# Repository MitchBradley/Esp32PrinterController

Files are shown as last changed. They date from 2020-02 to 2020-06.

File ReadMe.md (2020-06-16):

# ESP32 3D Printer Controller

This is based on https://github.com/felixstorm/Creality_Ender_3_ESP32_Board.git with the following changes

- Laid out for 2-sided PCB fabrication instead of PCB routing.  2-sided PCBs are available at very low cost from various prototyping shops, and provide much better grounding and power distribution.
- Can use either Pololu stepper driver modules or external drivers, selected by solder jumpers.
- The microstepping ratio can be selected by solder jumpers, or those pins can be connected to SPI for fine-grained configuration of TMC modules.  The X Y and Z axes all use the same microstepping/SPI settings, whereas the extruder can be configured independently of X, Y, Z.
- The I/O voltage to the shift registers and stepper modules can be either 3V3 or 5V, selected by solder jumper.  3V3 is appropriate for TMC modules where the SPI output goes back to the ESP32.  5V is best for external drivers whose optocoupler inputs work best at 5V.  Non-TMC stepper modules can use either.
- The micro SD card socket uses a Wemos D1 Mini shield which has a smaller footprint than the one on the original design, permitting all the drivers to be placed along one edge of the board.
- The connectors along the bottom edge of the board, and the power input connector, are all pluggable terminal blocks, thus permitting easy disconnection of the signals for assembly and maintenance.  The layout permits each signal pair to be on its own plug, or everything on one longer plug, or any combination thereof, at the users discretion.
- For the steppers, you can choose either 0.1" pitch connectors - e.g. pin headers with Dupont connectors - or 0.15" pitch pluggable terminal blocks (or 0.15" screw terminals, but pluggable is easier to wire and maintain).
- The fuse holders were spread out to make it easier to get your fingers in to grab the fuses.

The design passes acceptance checks for the aisler.net entry level prototyping service.

Update: The board is fully functional.  If you would like to build it, contact me and I will upload the revised version that fixes a few silkscreen errors and provides better clearance between some components that were a little crowded.

*Yet another Update:  Do not use the fan outputs; they are broken.  If you connect a fan it is likely to blow up the ULN2803A chip.  The problem - which I inherited from the base design and neglected to check - is that you cannot put ULN2803A channels in parallel and get them to share current.  ULN2803A use bipolar junction transistors - BJTs.  BJTs have a positive temperature coefficient, which means that, as the temperature increases, the collector current also increases.  When you put them in parallel, if one of them starts drawing a little more current than its neighbor, it gets hotter, and starts drawing even more current.  This is called "thermal runaway". Instead of sharing the load, one will take it all, then overheat and blow out, then the neighbor will take all the current and blow out, etc.  It is possible to make current-sharing circuits with BJTs, but ULN2803A does not have that kind of circuit.  The solution to the problem is to replace the ULN2803A with MOSFETs like that one that controls the extruder temperature.*

The board works with Marlin 2.0 for printer applications and with [Grbl_ESP32](https://github.com/bdring/Grbl_Esp32) for general CNC.

ESP32PrinterBoard

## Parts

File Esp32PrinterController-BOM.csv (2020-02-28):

Id | Designator | Package | Quantity | Designation | Supplier and ref
1 | J11 | PhoenixContact_MSTBVA_2,5_2-G-5,08_1x02_P5.08mm_Vertical_WallToWall | 1 | +BED-
2 | J1 | PhoenixContact_MSTBVA_2,5_2-G-5,08_1x02_P5.08mm_Vertical_WallToWall | 1 | -24V IN+
3 | J20 | PhoenixContact_MSTBVA_2,5_2-G-5,08_1x02_P5.08mm_Vertical_WallToWall | 1 | +BT-
4 | J21 | PhoenixContact_MSTBVA_2,5_2-G-5,08_1x02_P5.08mm_Vertical_WallToWall | 1 | +NT-
5 | J30 | PhoenixContact_MSTBVA_2,5_2-G-5,08_1x02_P5.08mm_Vertical_WallToWall | 1 | +XM-
6 | J31 | PhoenixContact_MSTBVA_2,5_2-G-5,08_1x02_P5.08mm_Vertical_WallToWall | 1 | +YM-
7 | J32 | PhoenixContact_MSTBVA_2,5_2-G-5,08_1x02_P5.08mm_Vertical_WallToWall | 1 | +ZM-
8 | J10 | PhoenixContact_MSTBVA_2,5_2-G-5,08_1x02_P5.08mm_Vertical_WallToWall | 1 | +NOZ-
9 | J12 | PhoenixContact_MSTBVA_2,5_2-G-5,08_1x02_P5.08mm_Vertical_WallToWall | 1 | +FAN1-
10 | J13 | PhoenixContact_MSTBVA_2,5_2-G-5,08_1x02_P5.08mm_Vertical_WallToWall | 1 | +FAN2-
11 | J14 | PhoenixContact_MSTBVA_2,5_2-G-5,08_1x02_P5.08mm_Vertical_WallToWall | 1 | +FAN3-
12 | U1 | MODULE_ESP32-DEVKITC-32D_LongPads | 1 | ESP32-DEVKITC-32D
13 | J60 | PinHeader_2x04_P2.54mm_Vertical | 1 | BLTouch
14 | J40 | PinHeader_2x05_P2.54mm_Vertical | 1 | LCD
15 | Q1 | TO-220-3_Vertical | 1 | IRLZ44N
16 | Q2 | TO-220-3_Vertical | 1 | IRLB8743
17 | JP15,JP2,JP3,JP4,JP5,JP6,JP7,JP10,JP11,JP12,JP13,JP14,JP16,JP17,JP18,JP19,JP20,JP21 | SolderJumper-2_P1.3mm_Open_TrianglePad1.0x1.5mm | 18 | SolderJumper_2_Open
18 | A2 | Pololu_Breakout-16_15.2x20.3mm | 1 | DRIVER_Y
19 | R16,R11 | R_Axial_DIN0207_L6.3mm_D2.5mm_P10.16mm_Horizontal | 2 | 100k
20 | D2 | LED_D5.0mm | 1 | NOZ
21 | D3 | LED_D5.0mm | 1 | BED
22 | R17,R12 | R_Axial_DIN0207_L6.3mm_D2.5mm_P10.16mm_Horizontal | 2 | 2.2k
23 | R15,R10 | R_Axial_DIN0207_L6.3mm_D2.5mm_P10.16mm_Horizontal | 2 | 10
24 | C4,C2,C21,C23,C30,C160,C32,C170,C31,C8,C9,C10,C11 | C_Rect_L7.2mm_W2.5mm_P5.00mm_FKS2_FKP2_MKS2_MKP2 | 13 | 0.1uF
25 | R22,R20 | R_Axial_DIN0207_L6.3mm_D2.5mm_P10.16mm_Horizontal | 2 | 4.7k
26 | H3,H4,H1,H2 | MountingHole_3mm | 4 | MountingHole
27 | D1 | D_DO-35_SOD27_P10.16mm_Horizontal | 1 | 1N5819
28 | U2 | Module_LM2596_DC-DC | 1 | DcStepDown_LM2596
29 | R30,R31,R32 | R_Axial_DIN0207_L6.3mm_D2.5mm_P10.16mm_Horizontal | 3 | 10k
30 | J6 | PhoenixContact_MCV_1,5_4-G-3.81_1x04_P3.81mm_Vertical | 1 | MOT E
31 | J25 | PhoenixContact_MCV_1,5_4-G-3.81_1x04_P3.81mm_Vertical | 1 | MOT X
32 | J26 | PhoenixContact_MCV_1,5_4-G-3.81_1x04_P3.81mm_Vertical | 1 | MOT Y
33 | J27 | PhoenixContact_MCV_1,5_4-G-3.81_1x04_P3.81mm_Vertical | 1 | MOT Z
34 | JP1 | SolderJumper-3_P2.0mm_Open_TrianglePad1.0x1.5mm_NumberLabels | 1 | Jumper_3_Open
35 | U6 | WEMOS_D1_mini_light | 1 | WeMos_D1_mini_SD_Shield
36 | JP8,JP9,JP22,JP23,JP24,JP25,JP26,JP27 | SolderJumper-3_P1.3mm_Open_RoundedPad1.0x1.5mm_NumberLabels | 8 | Jumper_3_Open
37 | J5 | PinHeader_1x04_P2.54mm_Vertical | 1 | MOT E
38 | J23 | PinHeader_1x04_P2.54mm_Vertical | 1 | MOT Y
39 | J24 | PinHeader_1x04_P2.54mm_Vertical | 1 | MOT Z
40 | A3 | Pololu_Breakout-16_15.2x20.3mm | 1 | DRIVER_Z
41 | A4 | Pololu_Breakout-16_15.2x20.3mm | 1 | DRIVER_E
42 | C5,C6,C7,C110,C1 | CP_Radial_D6.3mm_P2.50mm | 5 | 100uF
43 | C22,C20 | CP_Radial_D5.0mm_P2.00mm | 2 | 4.7uF
44 | A1 | Pololu_Breakout-16_15.2x20.3mm | 1 | DRIVER_X
45 | C3 | CP_Radial_D7.5mm_P2.50mm | 1 | 100uF
46 | F1 | Fuseholder_Blade_ATO_Littelfuse_Pudenz_2_Pin | 1 | 3A REM
47 | F2 | Fuseholder_Blade_ATO_Littelfuse_Pudenz_2_Pin | 1 | 10A BED
48 | J110 | PinHeader_1x04_P2.54mm_Vertical | 1 | MOT X
49 | U3,U4 | DIP-16_W7.62mm_Socket_LongPads | 2 | 74AHCT595
50 | U5 | DIP-18_W7.62mm_Socket_LongPads | 1 | ULN2803A

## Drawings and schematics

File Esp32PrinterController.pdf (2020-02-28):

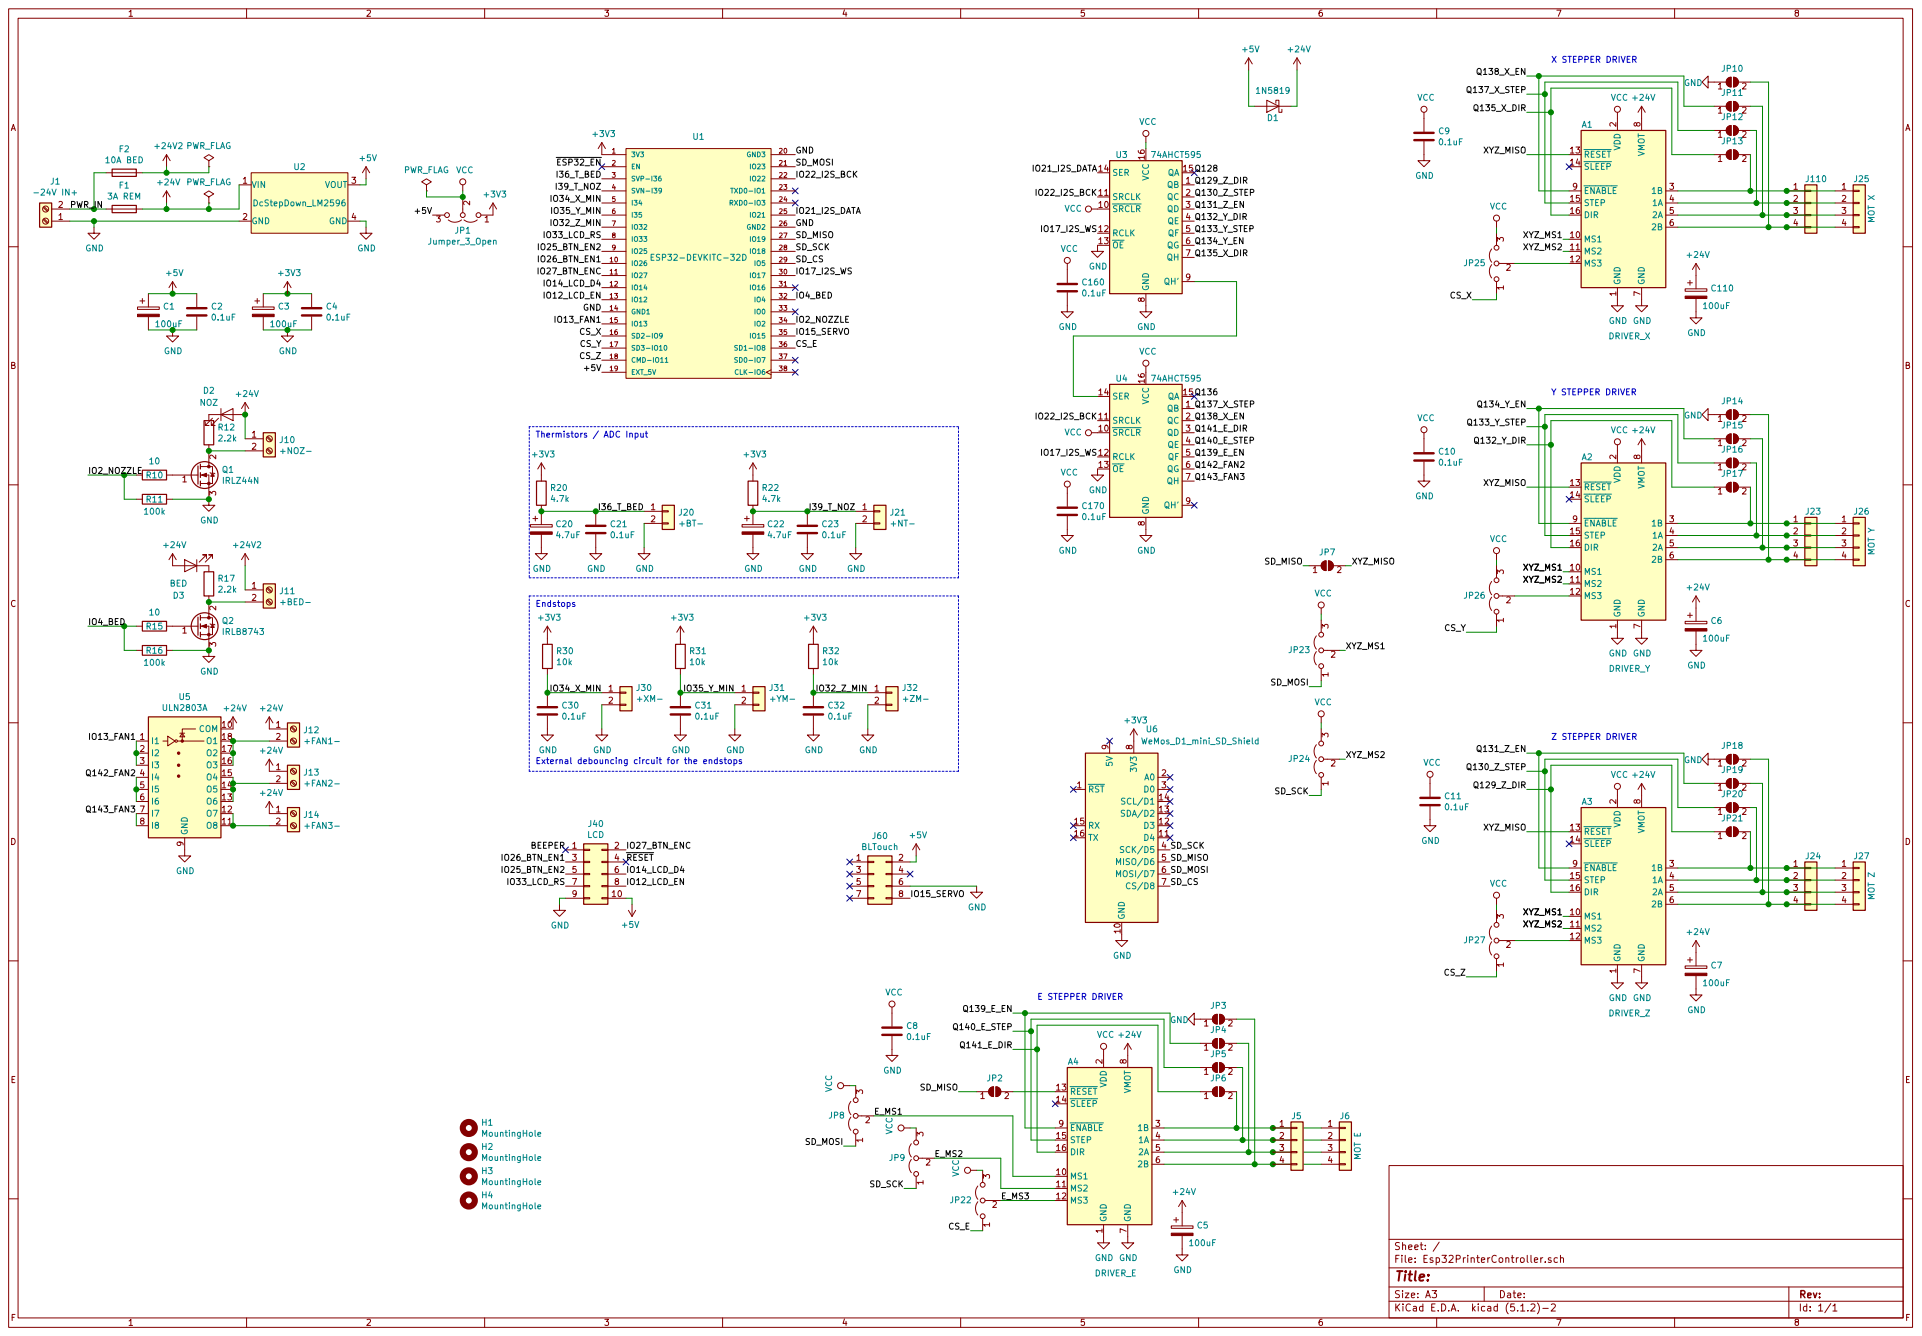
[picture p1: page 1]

1 MS1 10 MS2 11 MS3 12 RESET 13 SLEEP 14 STEP 15 DIR 16 VDD

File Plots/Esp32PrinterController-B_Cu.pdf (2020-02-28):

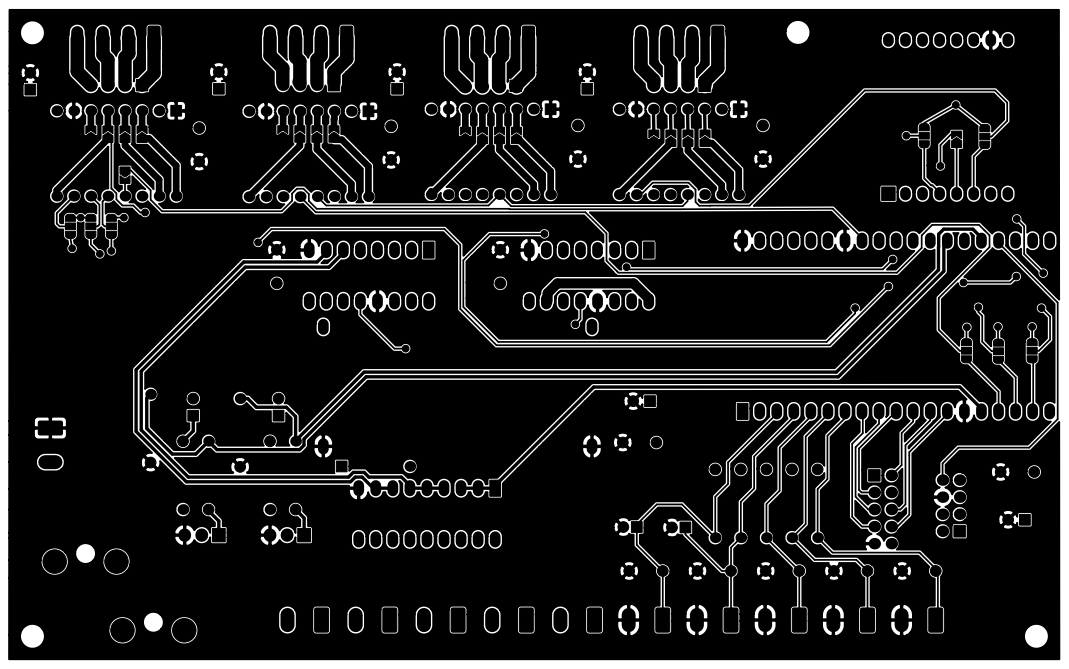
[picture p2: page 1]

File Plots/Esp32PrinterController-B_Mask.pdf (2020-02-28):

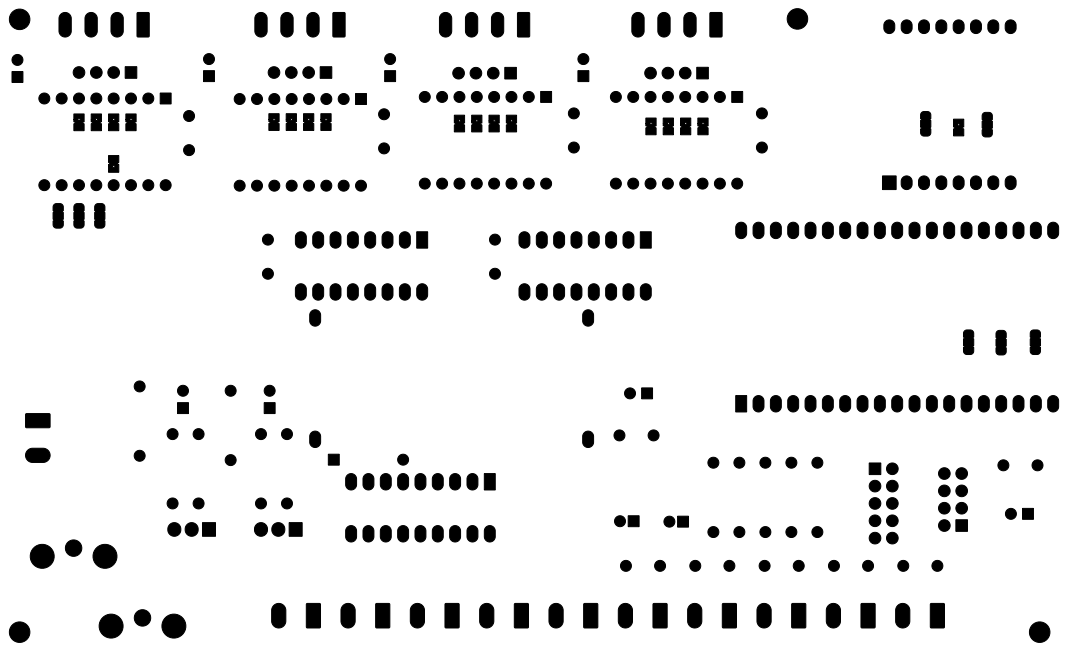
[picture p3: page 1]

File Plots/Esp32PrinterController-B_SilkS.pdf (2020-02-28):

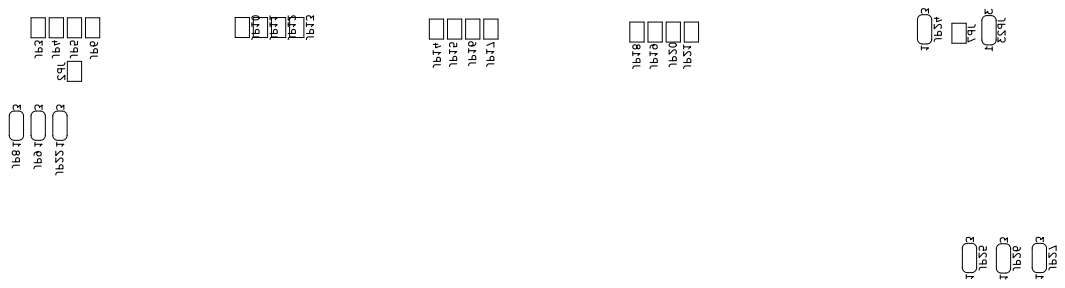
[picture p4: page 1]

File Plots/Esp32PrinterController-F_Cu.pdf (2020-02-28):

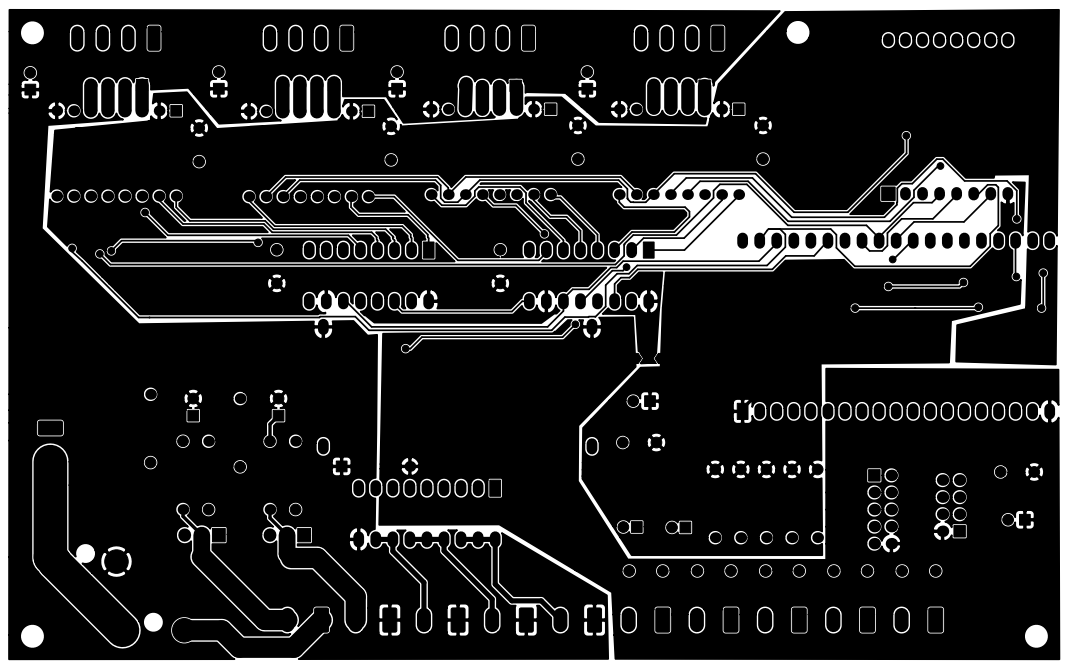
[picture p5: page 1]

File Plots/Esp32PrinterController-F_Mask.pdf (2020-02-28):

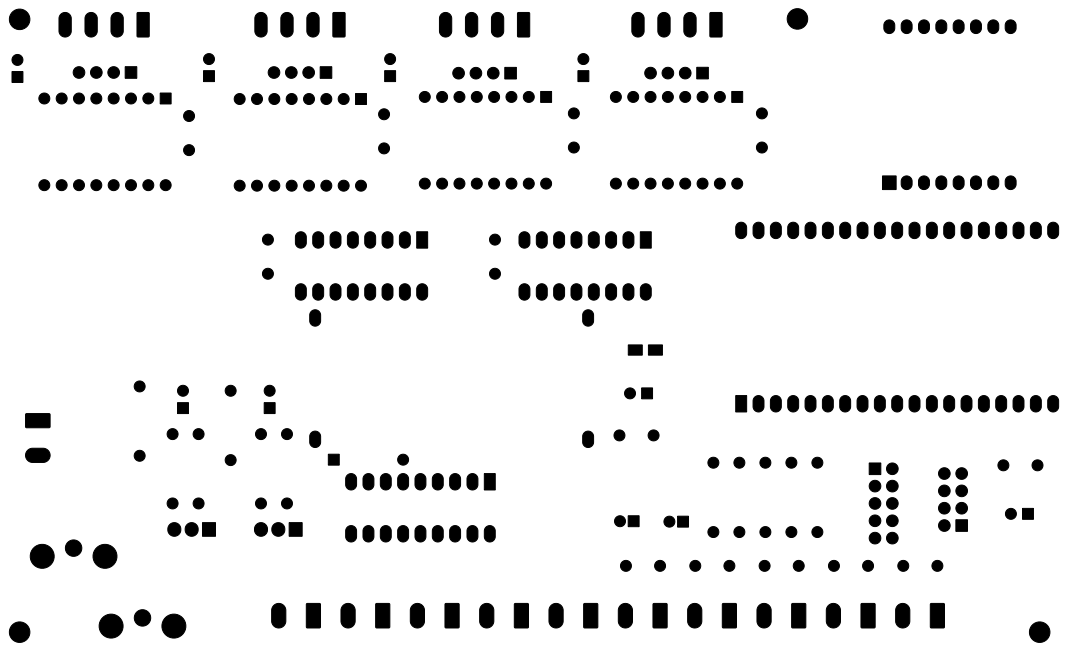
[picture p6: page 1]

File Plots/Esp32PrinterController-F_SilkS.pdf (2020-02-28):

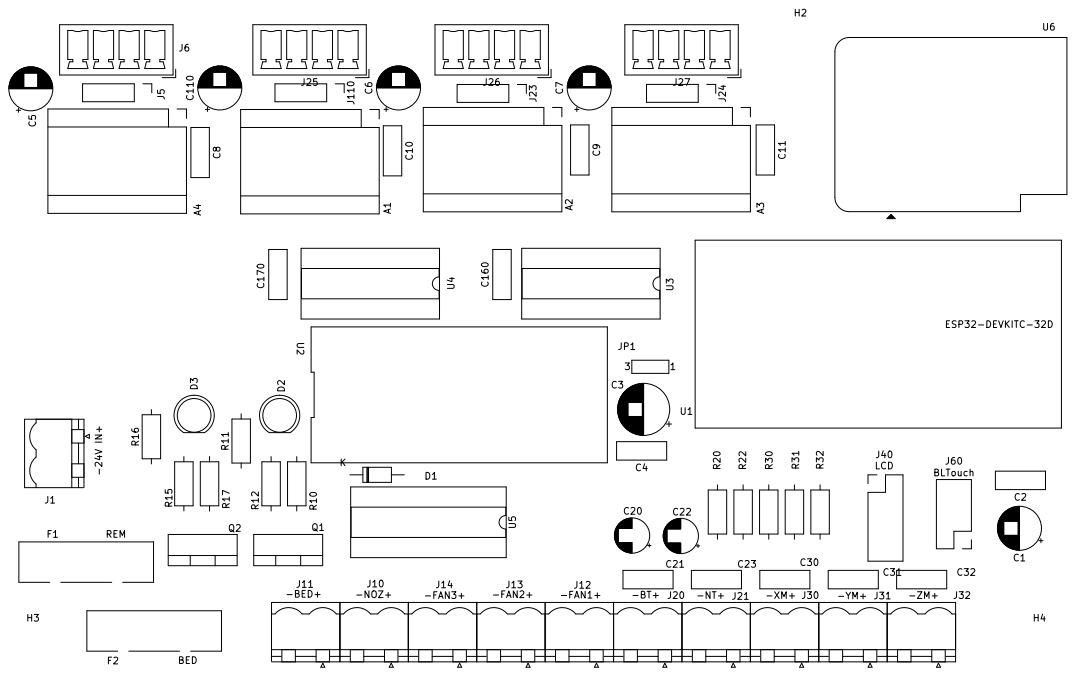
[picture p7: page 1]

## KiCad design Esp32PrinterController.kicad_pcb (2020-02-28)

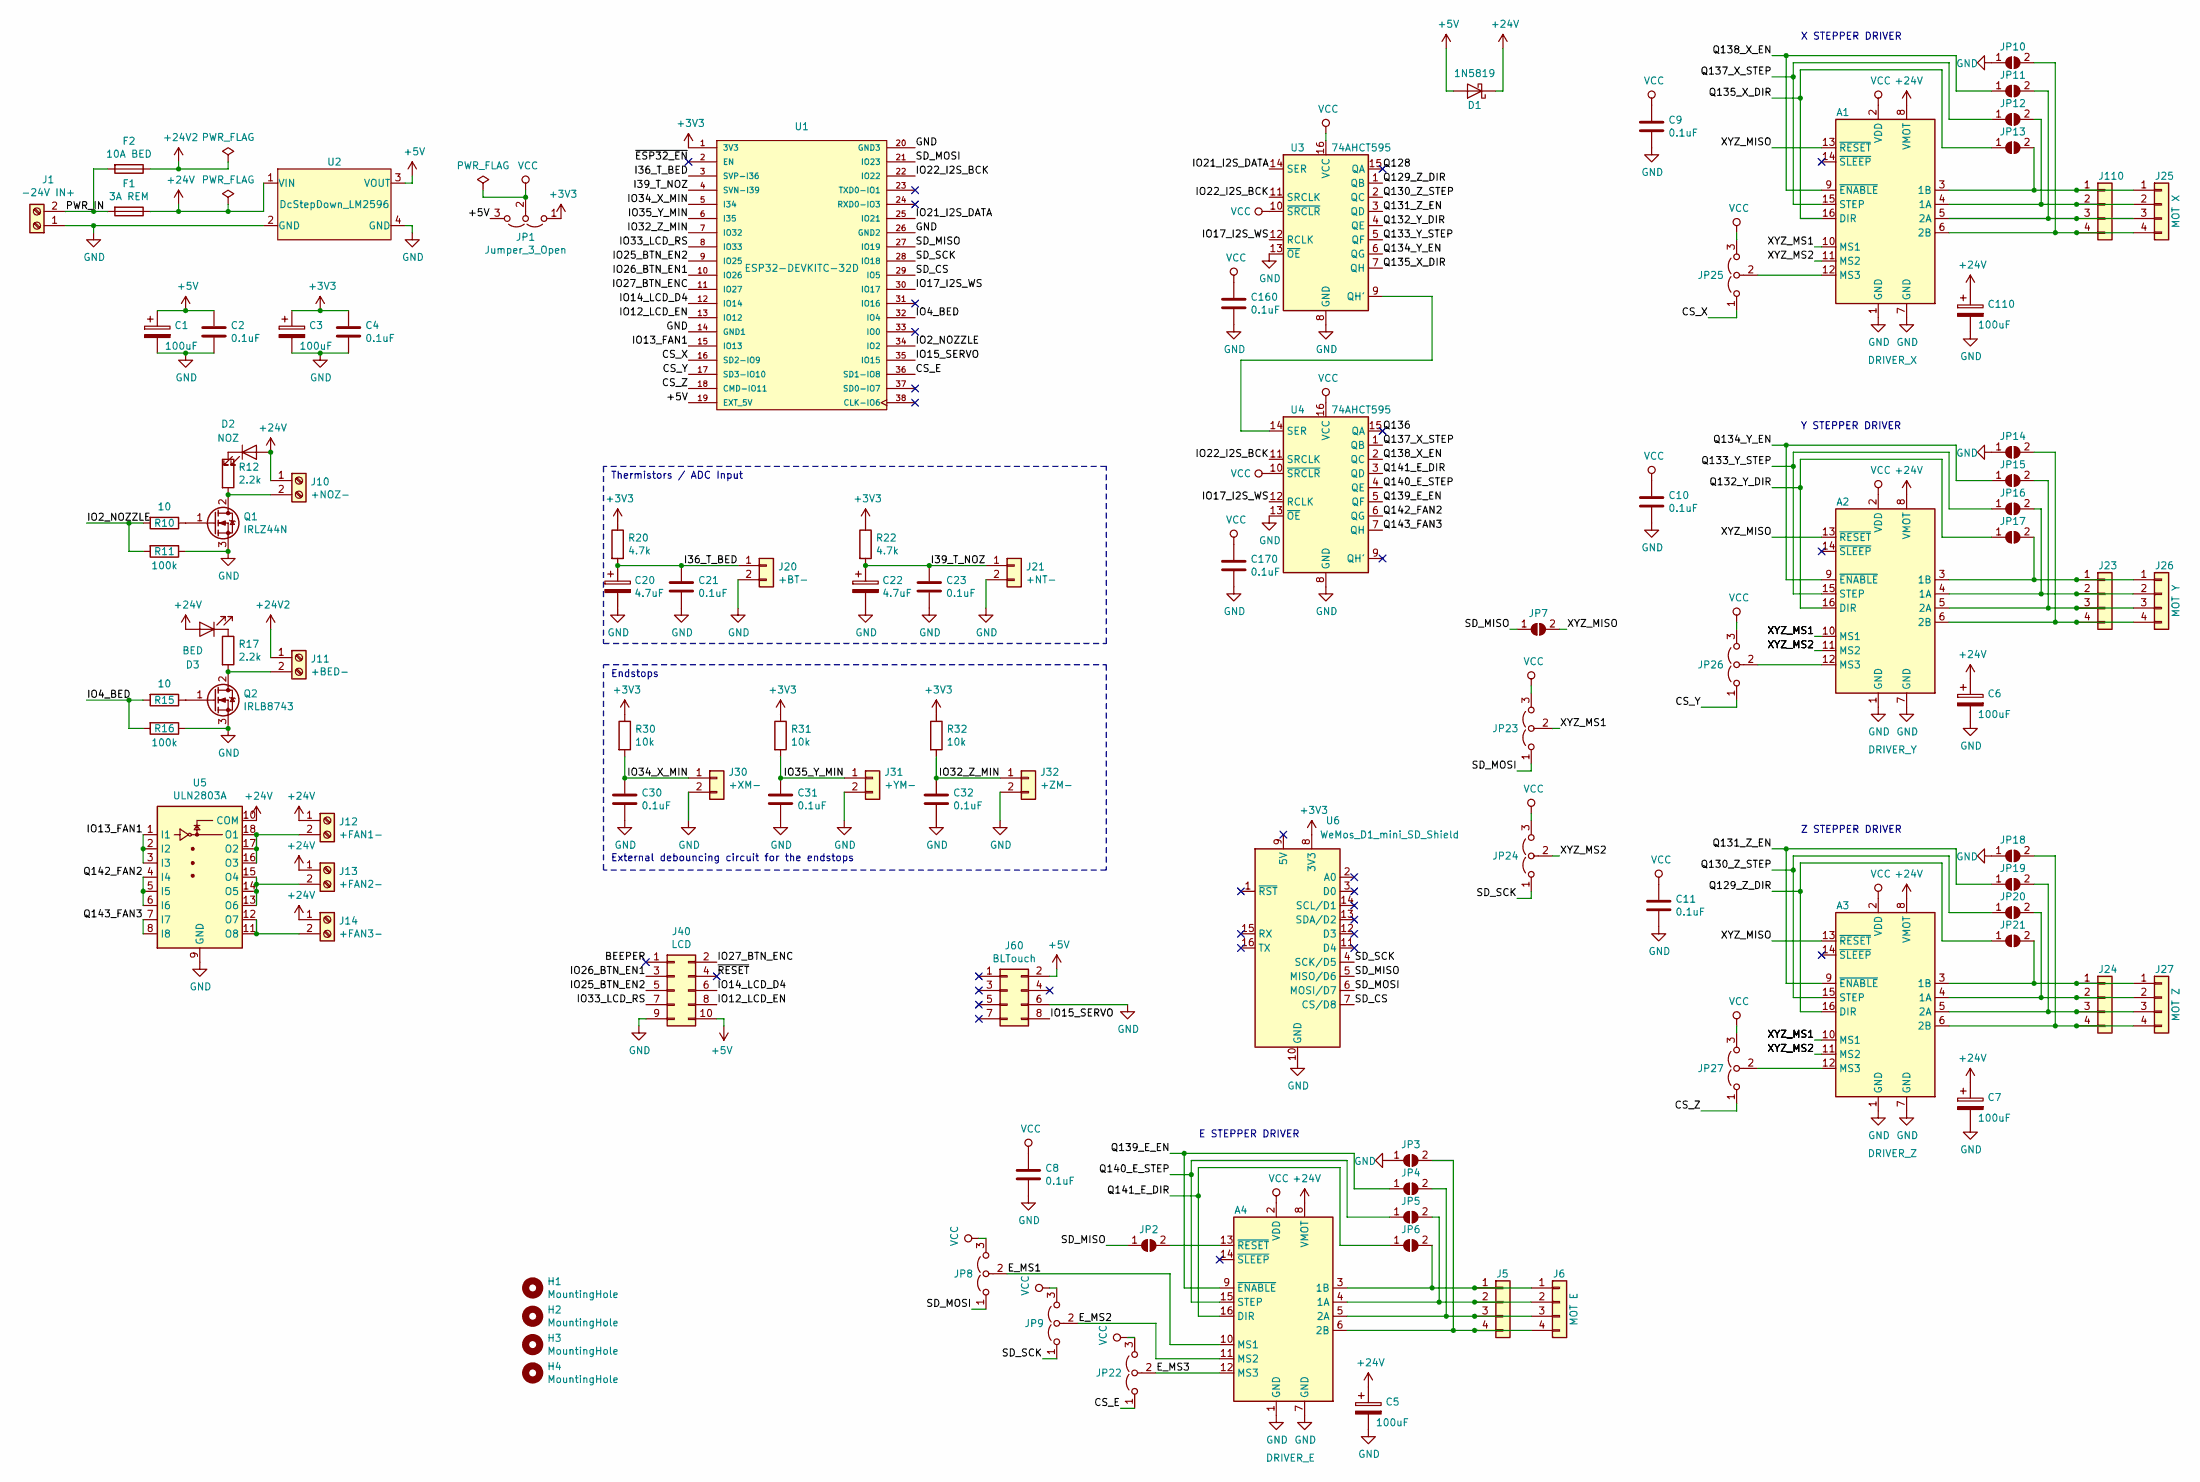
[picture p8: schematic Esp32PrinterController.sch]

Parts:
A1: DRIVER_X; Pololu_Breakout-16_15.2x20.3mm
A2: DRIVER_Y; Pololu_Breakout-16_15.2x20.3mm
A3: DRIVER_Z; Pololu_Breakout-16_15.2x20.3mm
A4: DRIVER_E; Pololu_Breakout-16_15.2x20.3mm
C1, C5, C6, C7, C110: 100uF; CP_Radial_D6.3mm_P2.50mm
C2, C4, C8, C9, C10, C11, C21, C23, C30, C31, C32, C160, C170: 0.1uF; C_Rect_L7.2mm_W2.5mm_P5.00mm_FKS2_FKP2_MKS2_MKP2
C3: 100uF; CP_Radial_D7.5mm_P2.50mm
C20, C22: 4.7uF; CP_Radial_D5.0mm_P2.00mm
D1: 1N5819; D_DO-35_SOD27_P10.16mm_Horizontal
D2: NOZ; LED_D5.0mm
D3: BED; LED_D5.0mm
F1: 3A REM; Fuseholder_Blade_ATO_Littelfuse_Pudenz_2_Pin
F2: 10A BED; Fuseholder_Blade_ATO_Littelfuse_Pudenz_2_Pin
H1, H2, H3, H4: MountingHole; MountingHole_3mm
J1: -24V IN+; PhoenixContact_MSTBVA_2,5_2-G-5,08_1x02_P5.08mm_Vertical
J5: MOT E; PinHeader_1x04_P2.54mm_Vertical
J6: MOT E; PhoenixContact_MCV_1,5_4-G-3.81_1x04_P3.81mm_Vertical
J10: +NOZ-; PhoenixContact_MSTBVA_2,5_2-G-5,08_1x02_P5.08mm_Vertical
J11: +BED-; PhoenixContact_MSTBVA_2,5_2-G-5,08_1x02_P5.08mm_Vertical
J12: +FAN1-; PhoenixContact_MSTBVA_2,5_2-G-5,08_1x02_P5.08mm_Vertical
J13: +FAN2-; PhoenixContact_MSTBVA_2,5_2-G-5,08_1x02_P5.08mm_Vertical
J14: +FAN3-; PhoenixContact_MSTBVA_2,5_2-G-5,08_1x02_P5.08mm_Vertical
J20: +BT-; PhoenixContact_MSTBVA_2,5_2-G-5,08_1x02_P5.08mm_Vertical
J21: +NT-; PhoenixContact_MSTBVA_2,5_2-G-5,08_1x02_P5.08mm_Vertical
J23: MOT Y; PinHeader_1x04_P2.54mm_Vertical
J24: MOT Z; PinHeader_1x04_P2.54mm_Vertical
J25: MOT X; PhoenixContact_MCV_1,5_4-G-3.81_1x04_P3.81mm_Vertical
J26: MOT Y; PhoenixContact_MCV_1,5_4-G-3.81_1x04_P3.81mm_Vertical
J27: MOT Z; PhoenixContact_MCV_1,5_4-G-3.81_1x04_P3.81mm_Vertical
J30: +XM-; PhoenixContact_MSTBVA_2,5_2-G-5,08_1x02_P5.08mm_Vertical
J31: +YM-; PhoenixContact_MSTBVA_2,5_2-G-5,08_1x02_P5.08mm_Vertical
J32: +ZM-; PhoenixContact_MSTBVA_2,5_2-G-5,08_1x02_P5.08mm_Vertical
J40: LCD; PinHeader_2x05_P2.54mm_Vertical
J60: BLTouch; PinHeader_2x04_P2.54mm_Vertical
J110: MOT X; PinHeader_1x04_P2.54mm_Vertical
JP1: Jumper_3_Open; SolderJumper-3_P2.0mm_Open_TrianglePad1.0x1.5mm_NumberLabels
JP2, JP3, JP4, JP5, JP6, JP7, JP10, JP11, JP12, JP13, JP14, JP15, JP16, JP17, JP18, JP19, JP20, JP21: SolderJumper_2_Open; SolderJumper-2_P1.3mm_Open_TrianglePad1.0x1.5mm
JP8, JP9, JP22, JP23, JP24, JP25, JP26, JP27: Jumper_3_Open; SolderJumper-3_P1.3mm_Open_RoundedPad1.0x1.5mm_NumberLabels
Q1: IRLZ44N; TO-220-3_Vertical
Q2: IRLB8743; TO-220-3_Vertical
R10, R15: 10; R_Axial_DIN0207_L6.3mm_D2.5mm_P10.16mm_Horizontal
R11, R16: 100k; R_Axial_DIN0207_L6.3mm_D2.5mm_P10.16mm_Horizontal
R12, R17: 2.2k; R_Axial_DIN0207_L6.3mm_D2.5mm_P10.16mm_Horizontal
R20, R22: 4.7k; R_Axial_DIN0207_L6.3mm_D2.5mm_P10.16mm_Horizontal
R30, R31, R32: 10k; R_Axial_DIN0207_L6.3mm_D2.5mm_P10.16mm_Horizontal
U1: ESP32-DEVKITC-32D; MODULE_ESP32-DEVKITC-32D_LongPads
U2: DcStepDown_LM2596; Module_LM2596_DC-DC
U3, U4: 74AHCT595; DIP-16_W7.62mm_Socket_LongPads
U5: ULN2803A; DIP-18_W7.62mm_Socket_LongPads
U6: WeMos_D1_mini_SD_Shield; WEMOS_D1_mini_light

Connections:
+3V3: C3.1, C4.1, JP1.1 (A), R20.1, R22.1, R30.1, R31.1, R32.1, U1.1 (3V3), U6.8 (3V3)
+5V: C1.1, C2.1, D1.2 (A), J40.10, J60.2, JP1.3 (B), U1.19 (EXT_5V), U2.3 (VOUT)
+24V: A1.8 (VMOT), A2.8 (VMOT), A3.8 (VMOT), A4.8 (VMOT), C5.1, C6.1, C7.1, C110.1, D1.1 (K), D2.2 (A), D3.2 (A), F1.1, J10.1, J12.1, J13.1, J14.1, U2.1 (VIN), U5.10 (COM)
+24V2: F2.1, J11.1
/BEEPER: J40.1
/CS_E: JP22.1 (A), U1.36 (SD1-IO8)
/CS_X: JP25.1 (A), U1.16 (SD2-IO9)
/CS_Y: JP26.1 (A), U1.17 (SD3-IO10)
/CS_Z: JP27.1 (A), U1.18 (CMD-IO11)
/E_MS1: A4.10 (MS1), JP8.2 (C)
/E_MS2: A4.11 (MS2), JP9.2 (C)
/E_MS3: A4.12 (MS3), JP22.2 (C)
/I36_T_BED: C20.1, C21.1, J20.1, R20.2, U1.3 (SVP-I36)
/I39_T_NOZ: C22.1, C23.1, J21.1, R22.2, U1.4 (SVN-I39)
/IO2_NOZZLE: R10.2, R11.2, U1.34 (IO2)
/IO4_BED: R15.2, R16.2, U1.32 (IO4)
/IO12_LCD_EN: J40.8, U1.13 (IO12)
/IO13_FAN1: U1.15 (IO13), U5.1 (I1), U5.2 (I2), U5.3 (I3)
/IO14_LCD_D4: J40.6, U1.12 (IO14)
/IO15_SERVO: J60.8, U1.35 (IO15)
/IO17_I2S_WS: U1.30 (IO17), U3.12 (RCLK), U4.12 (RCLK)
/IO21_I2S_DATA: U1.25 (IO21), U3.14 (SER)
/IO22_I2S_BCK: U1.22 (IO22), U3.11 (SRCLK), U4.11 (SRCLK)
/IO25_BTN_EN2: J40.5, U1.9 (IO25)
/IO26_BTN_EN1: J40.3, U1.10 (IO26)
/IO27_BTN_ENC: J40.2, U1.11 (IO27)
/IO32_Z_MIN: C32.1, J32.1, R32.2, U1.7 (IO32)
/IO33_LCD_RS: J40.7, U1.8 (IO33)
/IO34_X_MIN: C30.1, J30.1, R30.2, U1.5 (I34)
/IO35_Y_MIN: C31.1, J31.1, R31.2, U1.6 (I35)
/PWR_IN: F1.2, F2.2, J1.2
/Q128: U3.15 (QA)
/Q129_Z_DIR: A3.16 (DIR), JP21.1 (A), U3.1 (QB)
/Q130_Z_STEP: A3.15 (STEP), JP20.1 (A), U3.2 (QC)
/Q131_Z_EN: A3.9 (~ENABLE), JP19.1 (A), U3.3 (QD)
/Q132_Y_DIR: A2.16 (DIR), JP17.1 (A), U3.4 (QE)
/Q133_Y_STEP: A2.15 (STEP), JP16.1 (A), U3.5 (QF)
/Q134_Y_EN: A2.9 (~ENABLE), JP15.1 (A), U3.6 (QG)
/Q135_X_DIR: A1.16 (DIR), JP13.1 (A), U3.7 (QH)
/Q136: U4.15 (QA)
/Q137_X_STEP: A1.15 (STEP), JP12.1 (A), U4.1 (QB)
/Q138_X_EN: A1.9 (~ENABLE), JP11.1 (A), U4.2 (QC)
/Q139_E_EN: A4.9 (~ENABLE), JP4.1 (A), U4.5 (QF)
/Q140_E_STEP: A4.15 (STEP), JP5.1 (A), U4.4 (QE)
/Q141_E_DIR: A4.16 (DIR), JP6.1 (A), U4.3 (QD)
/Q142_FAN2: U4.6 (QG), U5.4 (I4), U5.5 (I5), U5.6 (I6)
/Q143_FAN3: U4.7 (QH), U5.7 (I7), U5.8 (I8)
/SD_CS: U1.29 (IO5), U6.7 (CS/D8)
/SD_MISO: JP2.1 (A), JP7.1 (A), U1.27 (IO19), U6.5 (MISO/D6)
/SD_MOSI: JP8.1 (A), JP23.1 (A), U1.21 (IO23), U6.6 (MOSI/D7)
/SD_SCK: JP9.1 (A), JP24.1 (A), U1.28 (IO18), U6.4 (SCK/D5)
/XYZ_MISO: A1.13 (~RESET), A2.13 (~RESET), A3.13 (~RESET), JP7.2 (B)
/XYZ_MS1: A1.10 (MS1), A2.10 (MS1), A3.10 (MS1), JP23.2 (C)
/XYZ_MS2: A1.11 (MS2), A2.11 (MS2), A3.11 (MS2), JP24.2 (C)
/~ESP32_EN: U1.2 (EN)
/~RESET: J40.4
GND: A1.1 (GND), A1.7 (GND), A2.1 (GND), A2.7 (GND), A3.1 (GND), A3.7 (GND), A4.1 (GND), A4.7 (GND), C1.2, C2.2, C3.2, C4.2, C5.2, C6.2, C7.2, C8.2, C9.2, C10.2, C11.2, C20.2, C21.2, C22.2, C23.2, C30.2, C31.2, C32.2, C110.2, C160.2, C170.2, J1.1, J20.2, J21.2, J30.2, J31.2, J32.2, J40.9, J60.6, JP3.1 (A), JP10.1 (A), JP14.1 (A), JP18.1 (A), Q1.3 (S), Q2.3 (S), R11.1, R16.1, U1.14 (GND1), U1.20 (GND3), U1.26 (GND2), U2.2 (GND), U2.4 (GND), U3.8 (GND), U3.13 (~OE), U4.8 (GND), U4.13 (~OE), U5.9 (GND), U6.10 (GND)
unnamed: A1.3 (1B), J25.1, J110.1, JP13.2 (B)
unnamed: A1.4 (1A), J25.2, J110.2, JP12.2 (B)
unnamed: A1.5 (2A), J25.3, J110.3, JP11.2 (B)
unnamed: A1.6 (2B), J25.4, J110.4, JP10.2 (B)
unnamed: A1.12 (MS3), JP25.2 (C)
unnamed: A2.3 (1B), J23.1, J26.1, JP17.2 (B)
unnamed: A2.4 (1A), J23.2, J26.2, JP16.2 (B)
unnamed: A2.5 (2A), J23.3, J26.3, JP15.2 (B)
unnamed: A2.6 (2B), J23.4, J26.4, JP14.2 (B)
unnamed: A2.12 (MS3), JP26.2 (C)
unnamed: A3.3 (1B), J24.1, J27.1, JP21.2 (B)
unnamed: A3.4 (1A), J24.2, J27.2, JP20.2 (B)
unnamed: A3.5 (2A), J24.3, J27.3, JP19.2 (B)
unnamed: A3.6 (2B), J24.4, J27.4, JP18.2 (B)
unnamed: A3.12 (MS3), JP27.2 (C)
unnamed: A4.3 (1B), J5.1, J6.1, JP6.2 (B)
unnamed: A4.4 (1A), J5.2, J6.2, JP5.2 (B)
unnamed: A4.5 (2A), J5.3, J6.3, JP4.2 (B)
unnamed: A4.6 (2B), J5.4, J6.4, JP3.2 (B)
unnamed: A4.13 (~RESET), JP2.2 (B)
unnamed: D2.1 (K), R12.1
unnamed: D3.1 (K), R17.1
unnamed: J10.2, Q1.2 (D), R12.2
unnamed: J11.2, Q2.2 (D), R17.2
unnamed: J12.2, U5.16 (O3), U5.17 (O2), U5.18 (O1)
unnamed: J13.2, U5.13 (O6), U5.14 (O5), U5.15 (O4)
unnamed: J14.2, U5.11 (O8), U5.12 (O7)
unnamed: Q1.1 (G), R10.1
unnamed: Q2.1 (G), R15.1
unnamed: U3.9 (QH'), U4.14 (SER)
VCC: A1.2 (VDD), A2.2 (VDD), A3.2 (VDD), A4.2 (VDD), C8.1, C9.1, C10.1, C11.1, C160.1, C170.1, JP1.2 (C), JP8.3 (B), JP9.3 (B), JP22.3 (B), JP23.3 (B), JP24.3 (B), JP25.3 (B), JP26.3 (B), JP27.3 (B), U3.10 (~SRCLR), U3.16 (VCC), U4.10 (~SRCLR), U4.16 (VCC)

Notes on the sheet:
X STEPPER DRIVER
Thermistors / ADC Input
Endstops
External debouncing circuit for the endstops
Y STEPPER DRIVER
Z STEPPER DRIVER
E STEPPER DRIVER

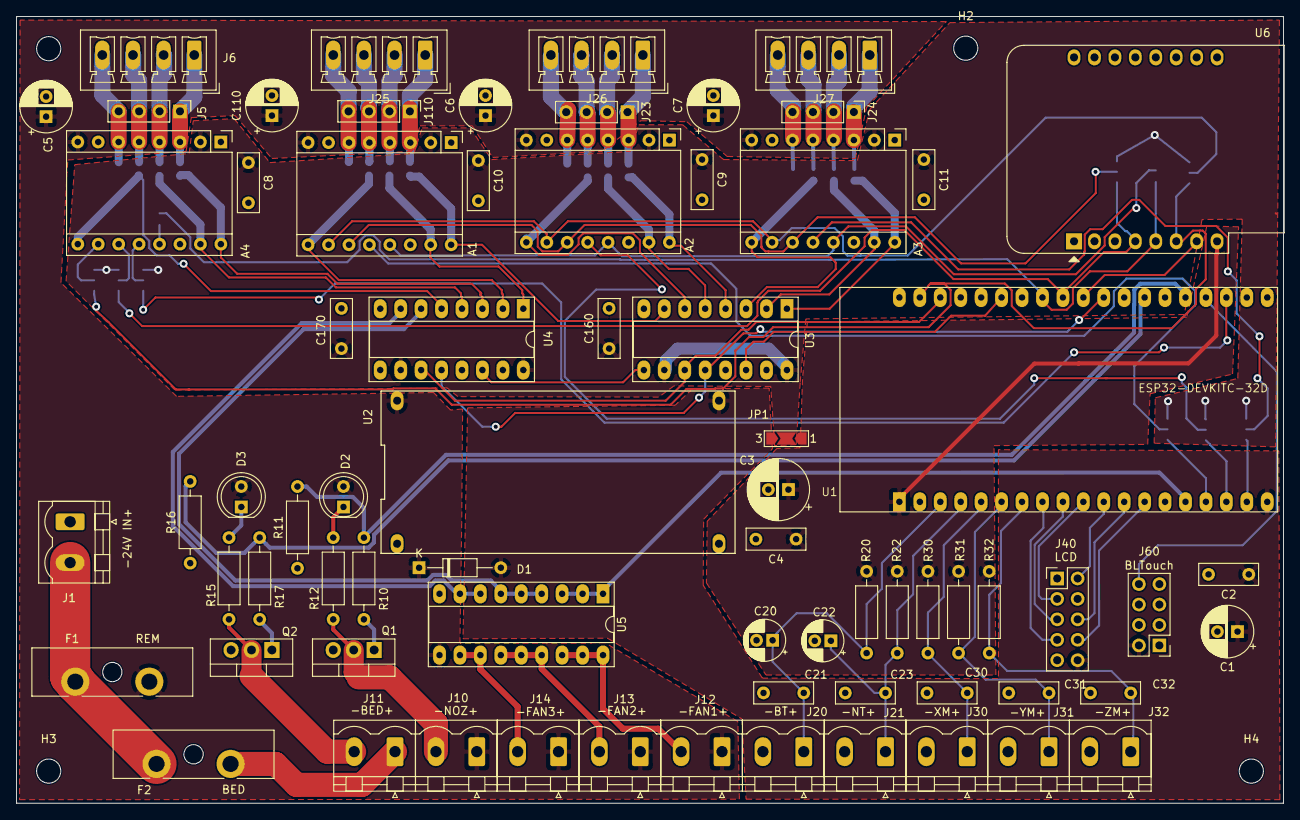
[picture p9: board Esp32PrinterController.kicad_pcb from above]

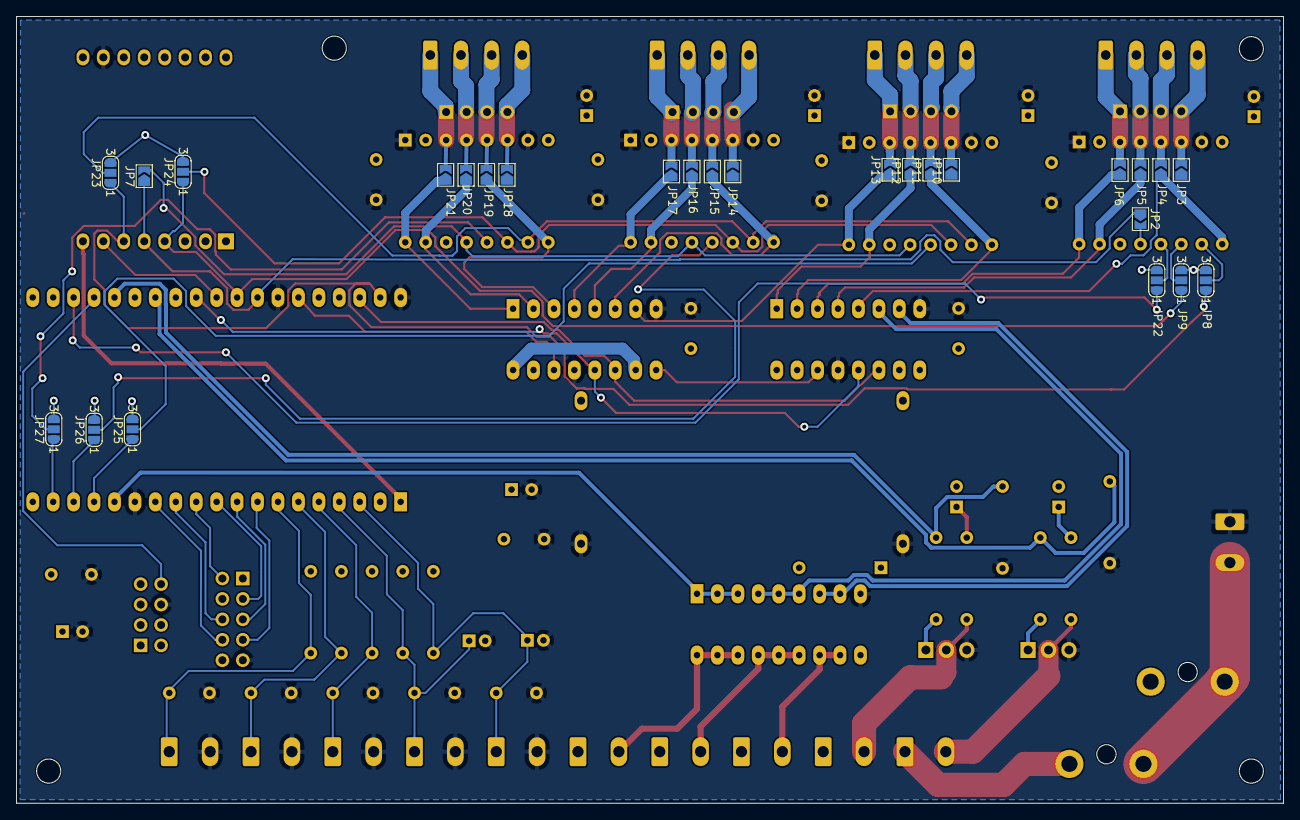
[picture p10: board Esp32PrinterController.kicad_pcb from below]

Board: 2 copper layers, 157.5 x 97.8 mm, 101 parts (26 on the bottom side), 83 nets.

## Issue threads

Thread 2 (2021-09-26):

Revised Board?

Shubham-0711, 2021-09-26:
I did not knew how to contact you for the revised edition, have you uploaded it already? if not, can you please do it. It'll be a great help.

MitchBradley, 2021-09-27:
I have abandoned work on this design in favor of Bart Dring's 6-pack design.  https://github.com/bdring/6-Pack_CNC_Controller

MitchBradley, 2021-09-27:
There is one major design flaw in the Esp32PrinterController.  The fan driving based on ULN2803 with outputs connected in parallel does not work as intended.  I copied that part of the circuit from the felixstorm design without checking it carefully.  The intention of paralleling the outputs was to provide more current than a single output can sink.  The problem is that ULN2803 has bipolar transistors, and bipolar transistors will not share current when they are connected in parallel (FETs will share, bipolars will not). With bipolars in parallel, the transistor with the lowest resistance will take the most current, heat up, and then take even more of the current, until it fails.  Then the next lowest resistance will do the same, until they all fail.  It happens very quickly.  The only safe way to use a ULN2803 is to use each channel to drive a separate load that is within the channel's current rating.

On my prototype boards, after one of the ULN2803s failed and I realized why, I removed the ULN2803s and replaced them with 3 logic-gate MOSFETs.

Shubham-0711, 2021-10-02:
Thank you for replying, I see the issue and I've read it before in your edits, it is really helpful of you to provide me with the work around for the issue. I'll work around that, But it'll be really helpful if I can also get the Configuration files used in the prototype for the Marlin Firmware as I want to test things and then assemble it into a printer and I don't want to use grbl because it's made for CNC only as far as I know. Best Regards.

MitchBradley, 2021-10-03:
What I have is in this branch https://github.com/MitchBradley/Marlin/tree/ESP32_Anycubic_i3  .  I haven't touched it in over a year so it is bound to be behind the Marlin curve.

MitchBradley, 2021-10-03:
I pushed my latest schematics to a new branch https://github.com/MitchBradley/Esp32PrinterController/tree/rev2 .  The pdfs and gerbers have not been updated, only the KiCad files.

Shubham-0711, 2021-10-03:
Ok, that would be great help. Thank you again for providing your guidance.

Closed 2021-10-03.

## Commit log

2020-02-28 Initial revision
    [Esp32PrinterController-BOM.csv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]
2020-05-12 Added photo and Grbl_ESP32 reference.
2020-06-16 Warn about fan bug
